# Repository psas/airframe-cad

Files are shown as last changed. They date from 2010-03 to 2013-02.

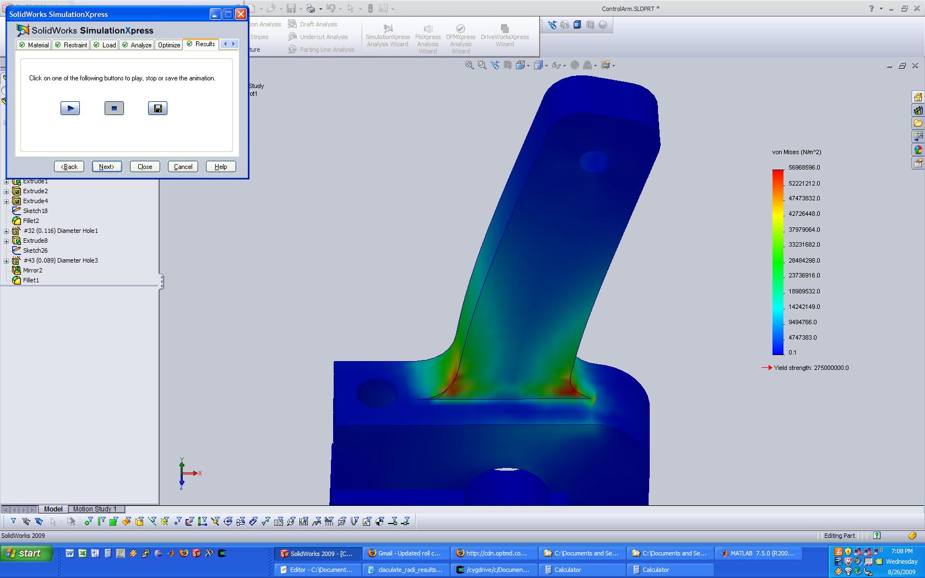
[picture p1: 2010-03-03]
sw_drawings/RollControl/FEA_Images/control_arm2.jpg

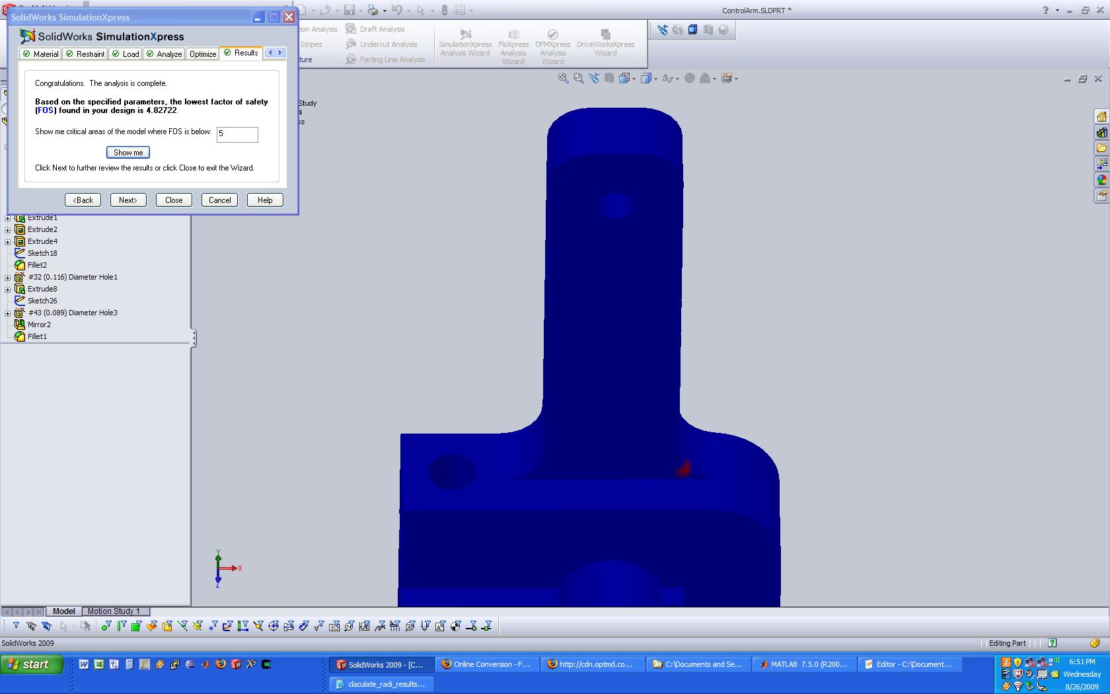
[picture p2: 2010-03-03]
sw_drawings/RollControl/FEA_Images/control_arm1.jpg

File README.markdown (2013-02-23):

# PSAS Airframe CAD files

Contains mostly solidworks files for the mechanical parts of our current rocket airframe.

 - [Airframe Team Home](http://psas.pdx.edu/airframe/)

You can download a free viewer from solidworks on their [downloads page](http://www.edrawingsviewer.com/ed/solidworks-viewer.htm).

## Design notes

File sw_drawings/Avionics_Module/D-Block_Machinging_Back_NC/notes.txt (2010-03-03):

1) uses 1/8 center drill
--X zero is the small flat side machined face of the endmost D-Block
--y-zero is the top face of the dblocks (back edge of vise) 
--z-zero is 1 inche above the machined faced side of the D-Block that were about to drill in

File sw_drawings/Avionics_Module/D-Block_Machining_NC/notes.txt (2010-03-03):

1) uses 1/2 roughing endmill
2-3) uses 1/2 finishing endmill
4) uses 1/8 center drill
5) uses 0.11dia drill

Zero is 1 inch above a piece of 0.5" x 5.0" x 2.0" flat bar, in the back-left corner of the stock

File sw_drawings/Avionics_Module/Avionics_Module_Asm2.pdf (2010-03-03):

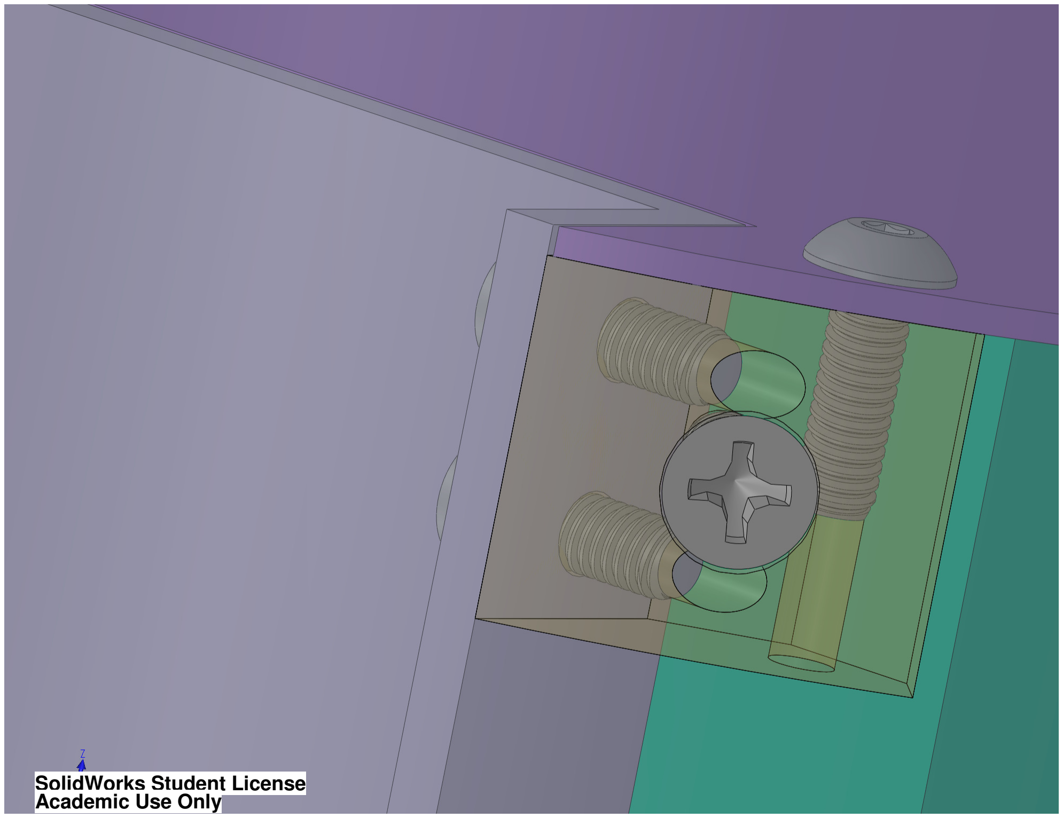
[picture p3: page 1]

SolidWorks Student License Academic Use Only

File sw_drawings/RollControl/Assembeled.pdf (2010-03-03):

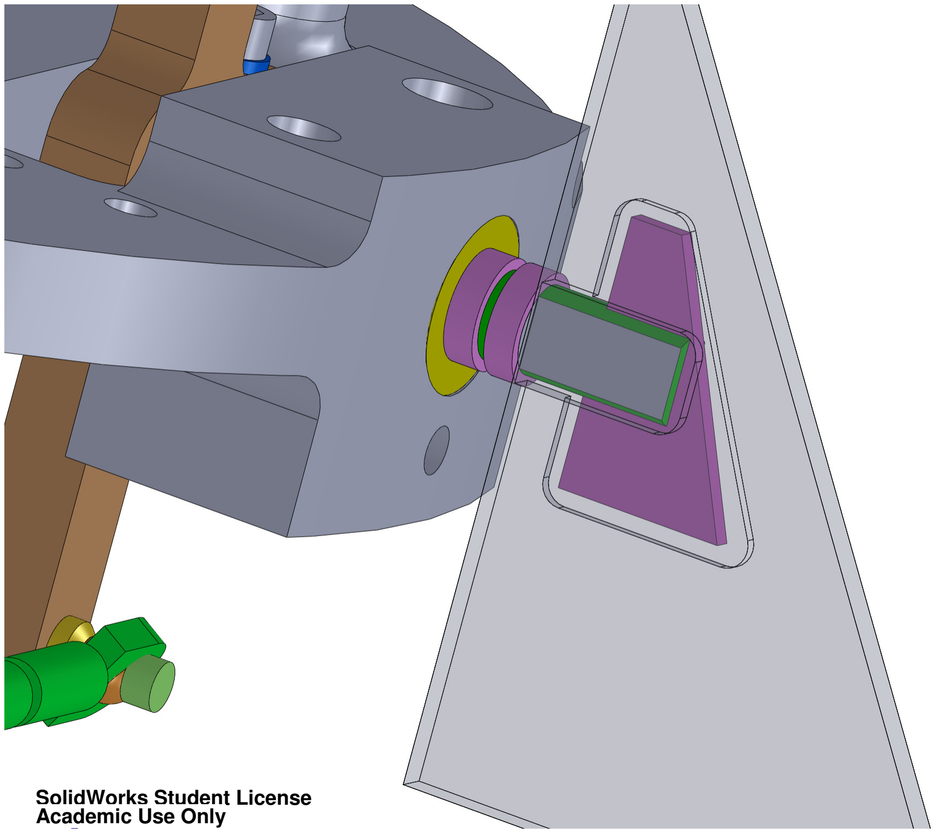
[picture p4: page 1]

SolidWorks Student License Academic Use Only

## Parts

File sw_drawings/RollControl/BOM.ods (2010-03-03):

Item | What for | Source | Source Part Number | Price | Qty | Ext Price
2-56 Dubro Swivel Ball Links | Linkage | Cyote Hobbies | LXAPC4 | $16.39 | 2 | $32.78
JR 8717 300hz Digital Servo | Linkage | Cyote Hobbies | JR 8717 | $109.00 | 1 | $109.00
1” by 0.375” 6061-T6 Flat bar, 3ft length | bell cranks | Master Carr | 8975K543 | $9.43 | 1 | $9.43
3mm screw, 18mm long, socket head cap screw | bell cranks | Master Carr | 91292A029 | $6.89 | 1 | $6.89
3mmID Tubing | bell cranks | Master Carr | 50415K158 | $11.65 | 1 | $11.65
3mmX6mmX2.5mm Ball Bearing | bell cranks | Master Carr | 7804K124 | $6.79 | 6 | $40.74
1/2” OD, 1/4” ID, 0.1875” thick ball bearings | Control Arm | Master Carr | 57155K376 | $5.10 | 8 | $40.80
1/4” ID Shaft Collar | Control Arm | Master Carr | 9414T6 | $0.58 | 4 | $2.32
1/4” OD Precision ground rod, hopefully machinable, 3ft section | Control Arm | Master Carr | 1144K16 |  | 1 | 0
4-40 Lock Nuts | Control Arm | Master Carr | 91831A005 | $3.95 | 1 | $3.95
4-40 socket head cap screw, 0.75” long | Control Arm | Master Carr | 92196A113 | $3.93 | 1 | $3.93
4-40 socket head cap screw, 1” long | Control Arm | Master Carr | 92196A115 | $4.00 | 1 | $4.00
4-40 Washers | Control Arm | Master Carr | 90945A711 | $13.05 | 1 | $13.05
Aluminum (Alloy 6061) Tube 1/2" OD, .402" ID, .049" Wall Thickness, 1' Length | Control Arm | Master Carr | 9056K653 | $5.96 | 1 | $5.96
Canard Spacer tubing | Control Arm | Master Carr | 8457K24 (http://www.mcmaster.com/itm/find.ASP?tab=find&context=psrchDtlLink&fasttrack=False&searchstring=8457K24) | $5.01 | 1 | $5.01
Woodruff Keys | Control Arm | Master Carr | 98525A050 | $6.01 | 1 | $6.01
2-56 Screws, 0.375” long, socket head cap | Linkage | Master Carr | 92196A079 | $3.72 | 1 | $3.72
2-56 Screws, 0.5” long, socket head cap | Linkage | Master Carr | 92196A081 | $3.97 | 1 | $3.97
2-56 Screws, 0.75” long, socket head cap | Linkage | Master Carr | 92196A084 | $4.64 | 1 | $4.64
2-56 Threaded rod, 1” sections | Linkage | Master Carr | 98804A003 | $1.72 | 1 | $1.72
2-56 Washers, a bag | Linkage | Master Carr | 98370A003 | $5.00 | 1 | $5.00
0.0625 thick, Silting saw that can do 0.671” deep, 3” or larger diameter | Tooling | Master Carr | 3061A35 | $23.60 | 1 | $23.60
C-2 Carbide Insert, 1/4" IC, 1/64" Radius | Tooling | Master Carr | 3240A132 | $5.13 | 2 | $10.26
Carbide-Insert Boring Tool 1/2" Shank Dia, 7/16" min Hole Dia, 2-1/8" D Max Bore | Tooling | Master Carr | 3249A202 | $25.59 | 1 | $25.59
Good 2-56 tap for aluminum | Tooling | Master Carr | 2636A116 | $12.40 | 1 | $12.40
Woodruff Cutter | Tooling | Master Carr | 3031A11 | $21.69 | 1 | $21.69
End mill, radius end mill, 0.125 radius, 0.5” dia, TiN | Tooling | MSC Direct | 8483075 | $69.03 | 1 | $69.03
End mill, TiN, 0.25” dia, standard end mill | Tooling | MSC Direct | 59517144 | $22.50 | 1 | $22.50
 |  |  |  |  |  |  |  | $499.64
6.0” OD, 1.75” thick, Aluminum 6061-T6 Round Bar | Base Plate | Metal Supermarkets |  | $18.17 | 1 | $18.17
3” x 0.25” x 36” 6061-T6 Flat Bar, if we need to machine control arms | Control Arm | Metal Supermarkets |  | $12.06 | 1 | $12.06
0.75” x 0.75” x 3ft 6061-T6 Square Bar | D-Blocks for mounting parts in modules | Metal Supermarkets |  | $8.89 | 1 | $8.89
18-8 Stainless Steel Nylon-Insert Hex Locknut 2-56 Thread Size, 1/4" Width, 9/64" Height | Linkage | Master Carr | 91831A002 | $13.62 | 1 | $13.62
E-Clips, Black-Phosphate Steel E-Style Retaining Ring for 1/4" Shaft Diameter | Control Arm | Master Carr | 97431A300 | $5.48 | 1 | $5.48
18-8 SS Precision Bearing Spacing Shim .020" Thick, .167" ID, .248" OD | Shims for aligning fins | Master Carr | 93574A213 | 7.81 | 1 | 7.81
8-8 SS Precision Bearing Spacing Shim .010" Thick, .167" ID, .248" OD | Shims for aligning fins | Master Carr | 93574A211 | 7.81 | 1 | 7.81
18-8 SS Precision Bearing Spacing Shim .005" Thick, .167" ID, .248" OD | Shims for aligning fins | Master Carr | 93574A207 | 7.81 | 1 | 7.81
 |  |  |  |  |  |  | $42.53
Plates for canards |  | Master Carr | 9517K112
Dubro Swivel Ball Links 2-56 (12) | Linkage | www.towerhobbies.com | LXAPC4 | $16.39 | 2 | $32.78

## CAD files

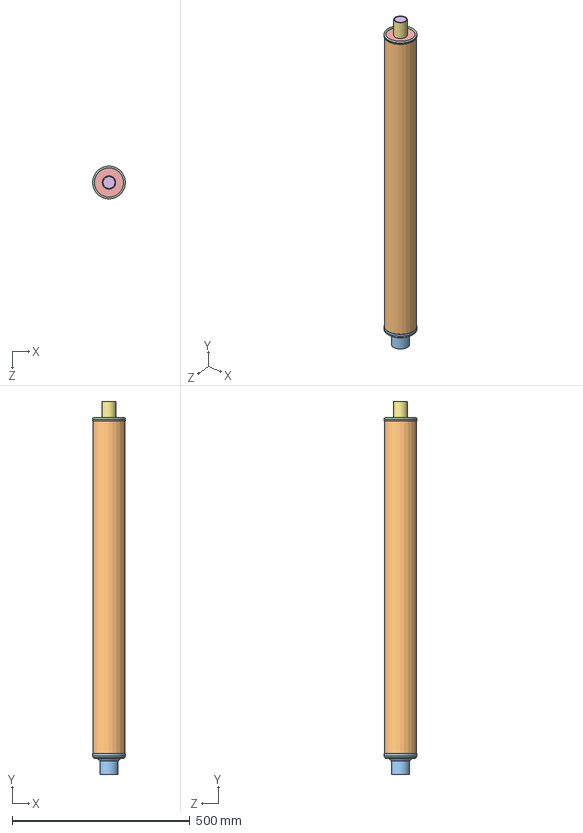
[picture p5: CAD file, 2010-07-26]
sw_drawings/Airframe_Drawings/N2000W_Motor_Reload/N2000W_Reload_Assembeled.SLDASM
92.2 x 1050.0 x 92.2 mm
N2000W_Grain x 6
N2000W_Reload_Liner
N2000W_Nozel
N2000W_O_Ring x 2
N2000W_Forward_Seal_Disc
N2000W_Smoke_Grain
N2000W_Smoke_Grain_Liner

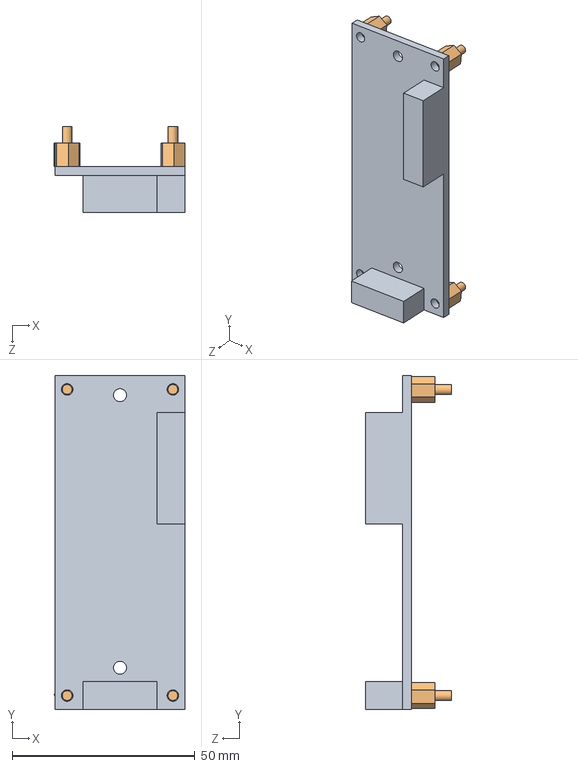
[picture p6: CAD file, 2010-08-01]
sw_drawings/Avionics/ARTS2_Flight_Computer_Asm.SLDASM
35.8 x 91.4 x 23.6 mm
ARTS2_Flight_Computer
0.25in_PCB_Standoff x 4

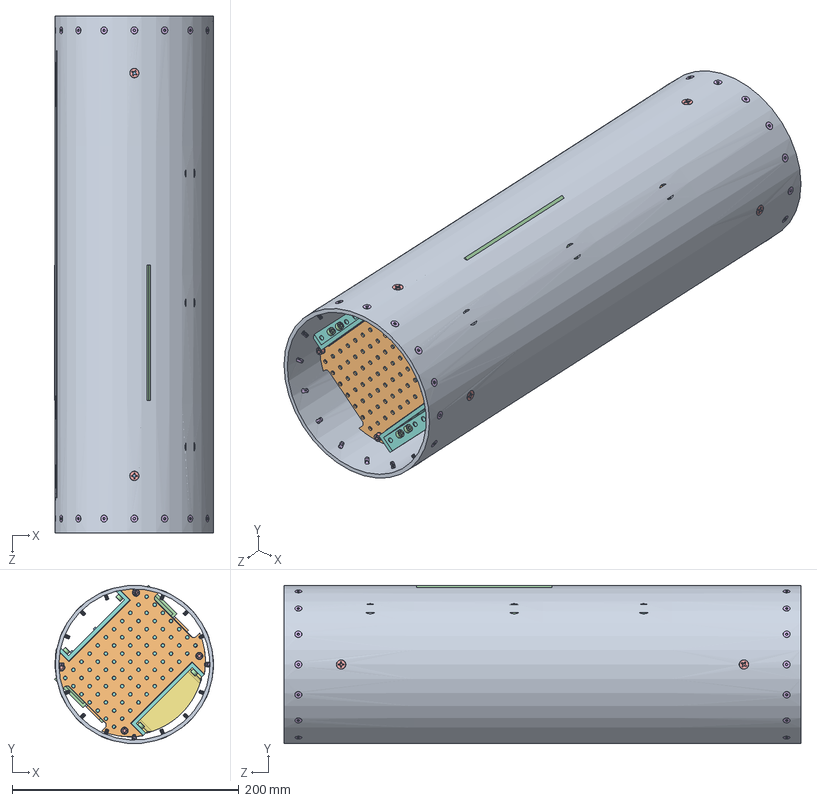
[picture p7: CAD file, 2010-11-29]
sw_drawings/Avionics_Module/Avionics_Module_Asm.SLDASM
140.5 x 139.9 x 456.4 mm
Avionics_Module_Plate2 x 3
D_Block_5 x 16
6-32_0.375in_Allen_Head_Cap_Screw_MC-91251A146 x 32
6-32_0.5in_Allen_Head_Cap_Screw_MC-91251A148 x 8
No_6_Steel_Wahser_MC-98032A436 x 8
RF_Sheild_Plate_SM
3in_x_0.6in_Channel_MC-9001K41 x 2
Mid_Plate
Mid_Plate_Angle x 2
4-40_Lock_Nut-MC-90631A005 x 8
Olimex_LPC2378
0.15in_Spacer x 4
4-40_0.3125in_Allen_Head_Cap_Screw_MC-91251A107 x 4
4-40_0.3125in_Pan_Head_Allen Cap_Screw_MC-91255A107 x 4
6-32_1.25in_Allen_Head_Cap_Screw_MC-91251A155 x 4
No_6_Steel_Wahser2_MC-94744A160 x 4
ARTS2_Flight_Computer
0.25in_PCB_Standoff x 4
Data_Logger
8-32_0.5in_Countersunk_Head_Allen_Screw-MC-91771A194_2 x 7
3.0mm_8mm_Counter_Sunk_Hex_Screw x 32
Battery_Box_Case
Battery_Box_Lid
Battery_Box_PCB_Board

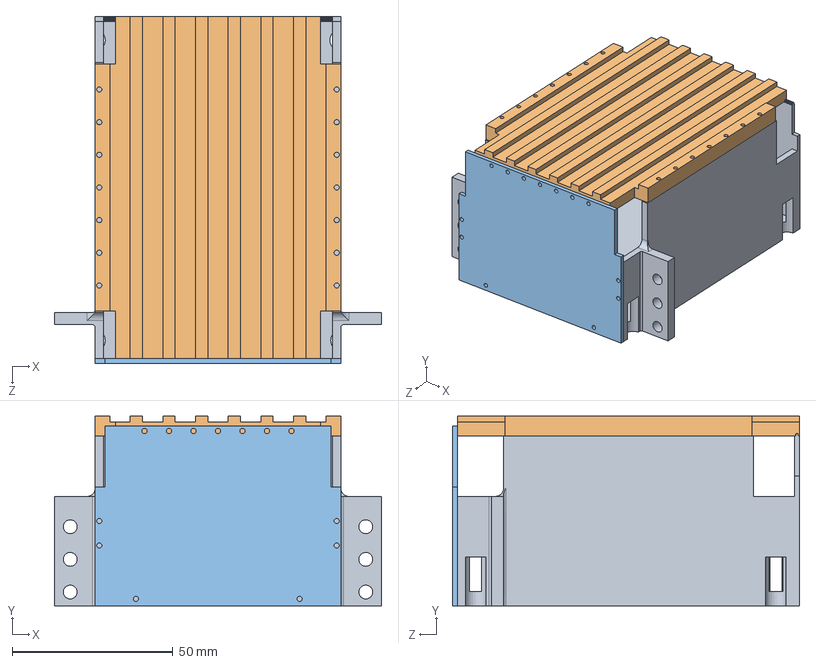
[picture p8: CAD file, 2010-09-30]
sw_drawings/Avionics_Module/Battery_Box/Battery_Box_Asm.SLDASM
101.9 x 59.1 x 108.0 mm
Battery_Box_Case
Battery_Box_Lid
Battery_Box_PCB_Board

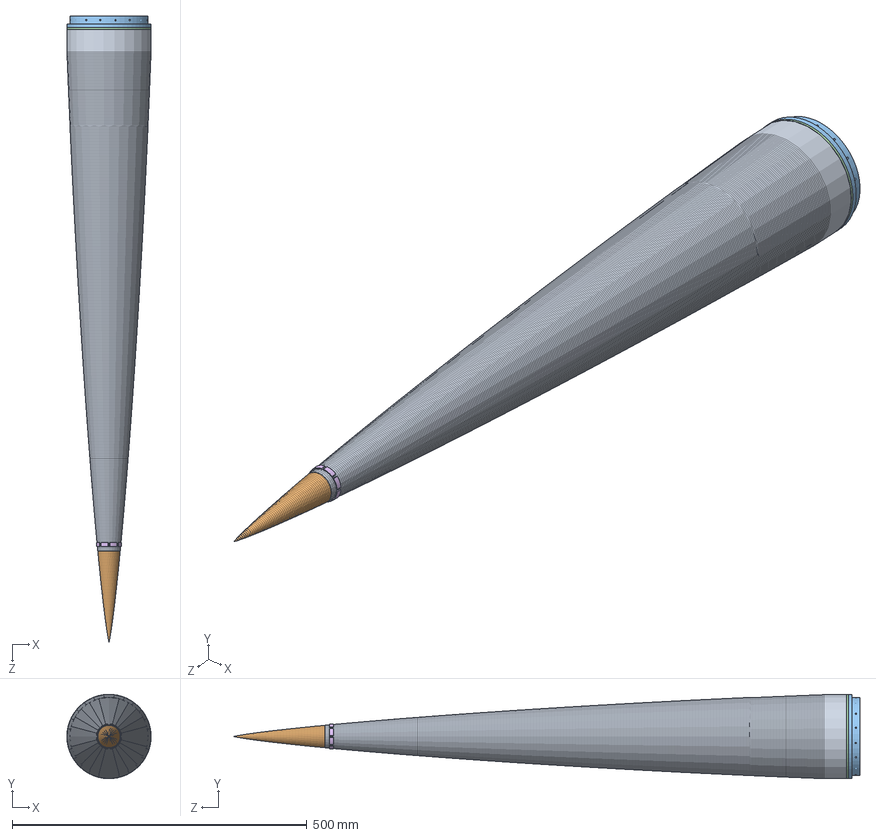
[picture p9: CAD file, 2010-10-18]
sw_drawings/Nosecone/Nosecone_Asm.SLDASM
143.1 x 143.1 x 1061.5 mm
Nosecone
Nosecone_Tip
NSR_Bottom
NSR_Top
Drogue_Parachute
Tip_Ring
Elastic_Outer_Ring
Pusher_Plate
Pusher_Tube
Upper_Elastic_Ring
Elastic x 23
8-32_Eyebolt

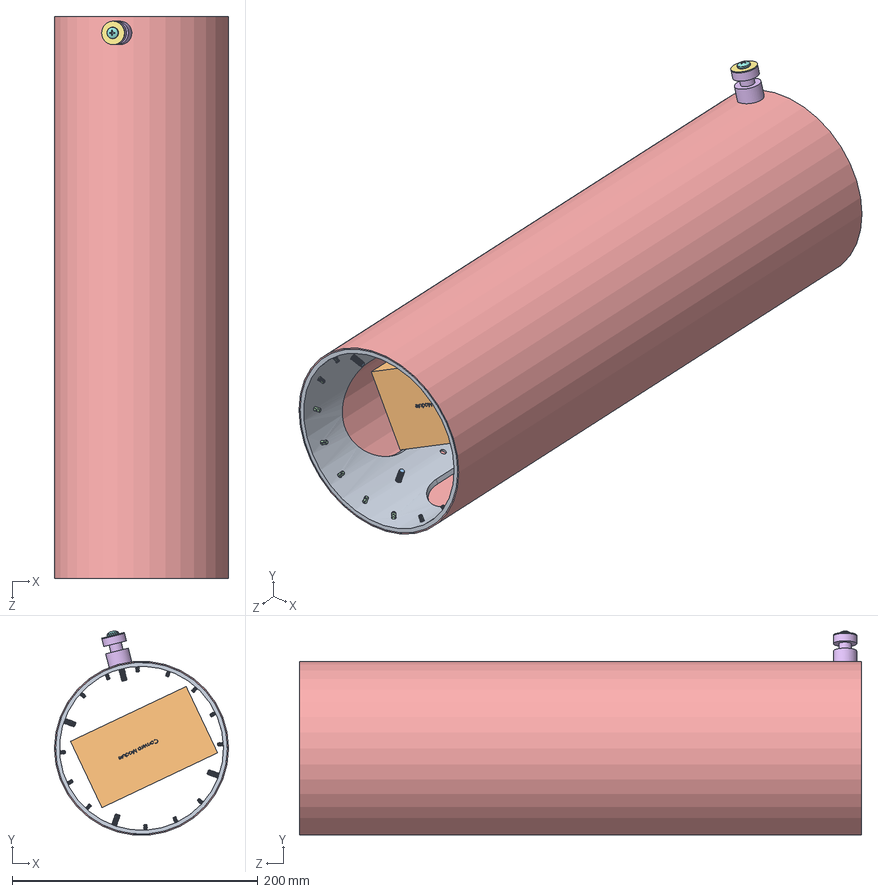
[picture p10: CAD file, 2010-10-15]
sw_drawings/Payload_Module/Payload_Module_Asm.SLDASM
141.6 x 165.9 x 457.2 mm
Module_Hollow
Camera_Module
8-32_0.5in_Countersunk_Head_Allen_Screw-MC-91771A194_2 x 6
3.0mm_8mm_Counter_Sunk_Hex_Screw x 32
Aeroshell_18
Launch_Lug
No_10_Steel_Fender_washer
10-32_1.5in_SS_Philips_Pan_Head_Screw

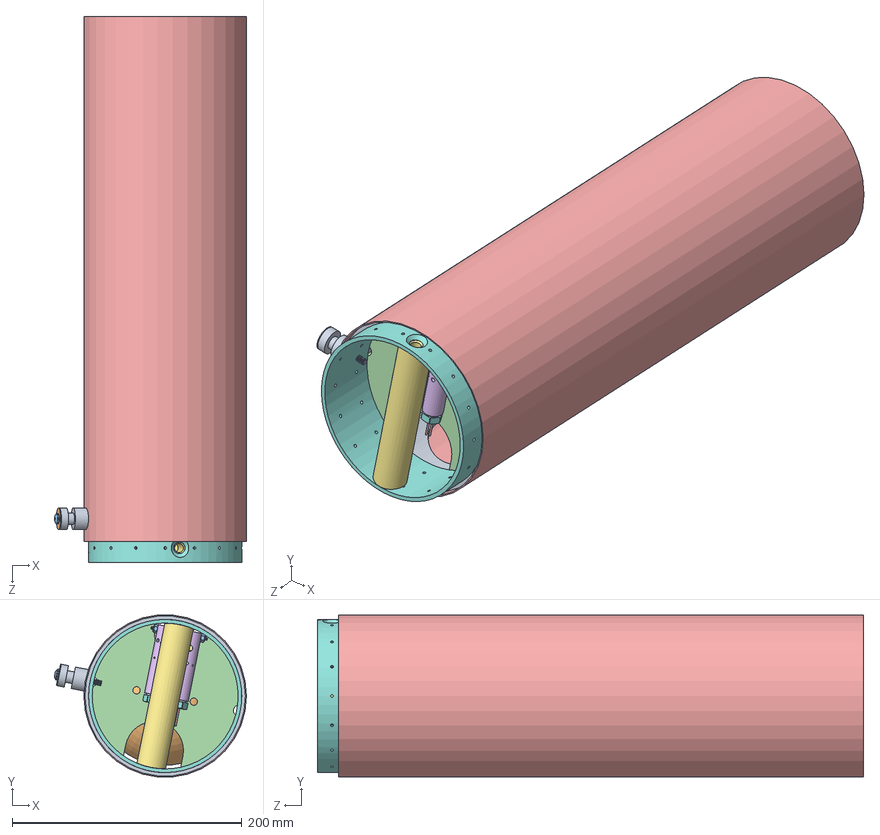
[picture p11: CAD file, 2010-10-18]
sw_drawings/Recovery_Module/Recovery_Module_Asm.SLDASM
167.2 x 141.0 x 475.5 mm
Module_Hollow_Short
Parachute
3.0mm_8mm_Counter_Sunk_Hex_Screw x 2
Shield_Plate
Line_Cutter_Body x 2
Cutter x 2
Modified_0.375in_x_0.5in_Hex_Head_Bolt x 2
Sealing_Washer x 2
Stop_Block x 2
4-40_Lock_Nut-MC-90631A005 x 2
4-40_0.875_Counter_Sunk_Cap_Screw x 2
Igniter_Lead_Wire x 4
Igniter x 2
Parachute_Cross_Bar
Module_Coupler_Recovery
Launch_Lug
No_10_Steel_Fender_washer
10-32_1.5in_SS_Philips_Pan_Head_Screw

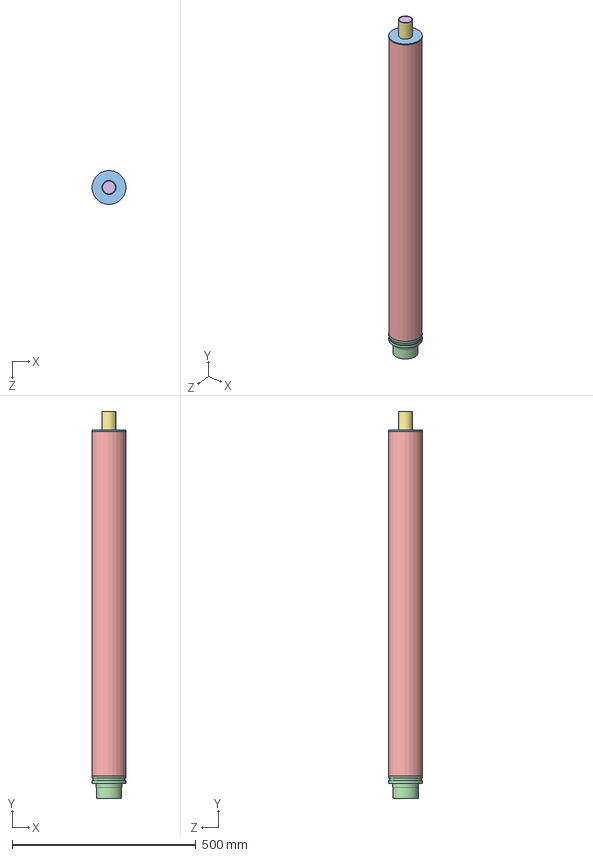
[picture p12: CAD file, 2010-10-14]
sw_drawings/Airframe_Drawings/N2850-P_Cesaroni_Reload/N2850_Reload_Asm.SLDASM
92.1 x 1052.3 x 92.1 mm
N2850P_Grain x 6
N2850P_Grain_O_Ring x 5
N2850P_Forward_Seal_Disc
N2850P_Nozel
N2850P_Reload_Liner
N2850P_Smoke_Grain
N2850P_Smoke_Grain_Liner

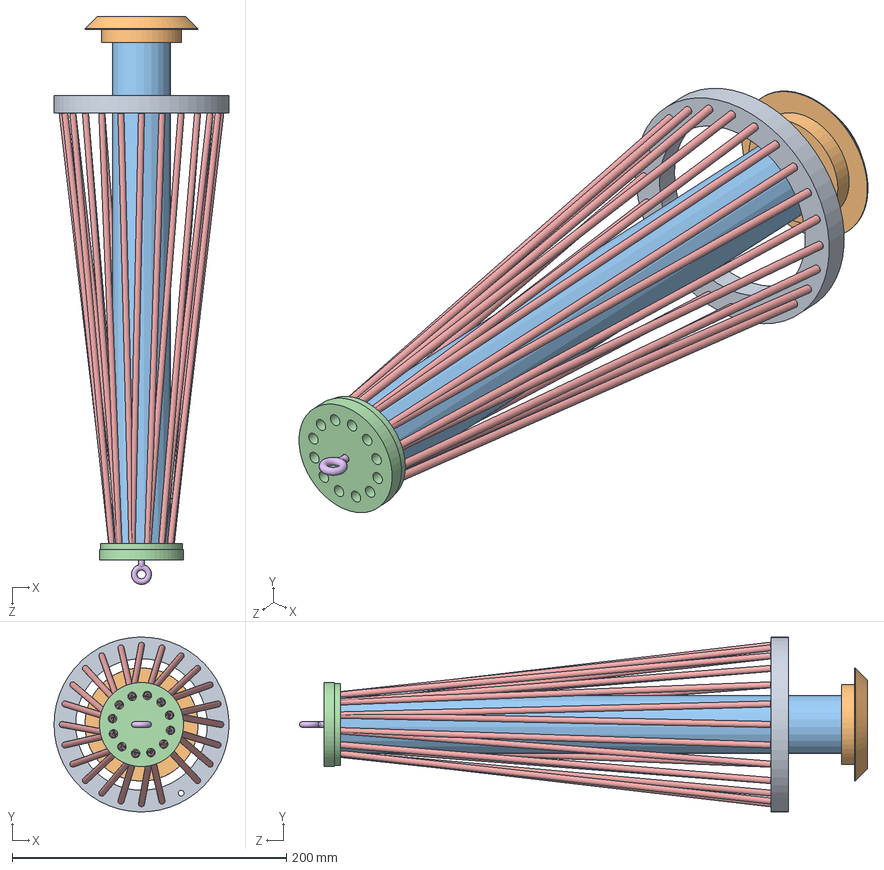
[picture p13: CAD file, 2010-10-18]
sw_drawings/Airframe_Drawings/Pusher_Rod/Pusher_Asm.SLDASM
127.7 x 127.6 x 414.5 mm
Elastic_Outer_Ring
Pusher_Plate
Pusher_Tube
Upper_Elastic_Ring
Elastic x 23
8-32_Eyebolt

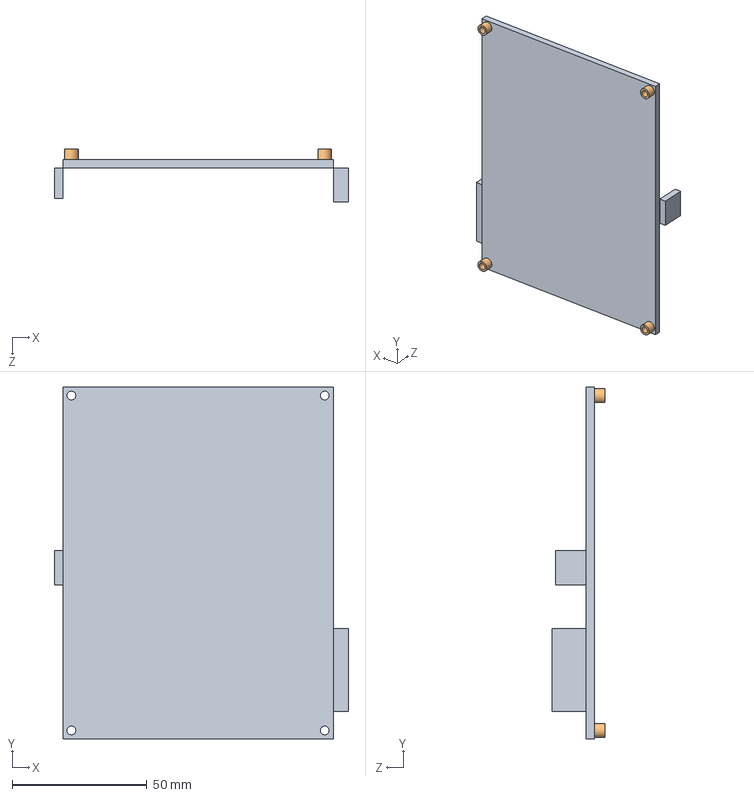
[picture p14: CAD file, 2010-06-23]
sw_drawings/Avionics/Olimex_2378_Asm.SLDASM
109.1 x 130.4 x 19.7 mm
Olimex_LPC2378
0.15in_Spacer x 4

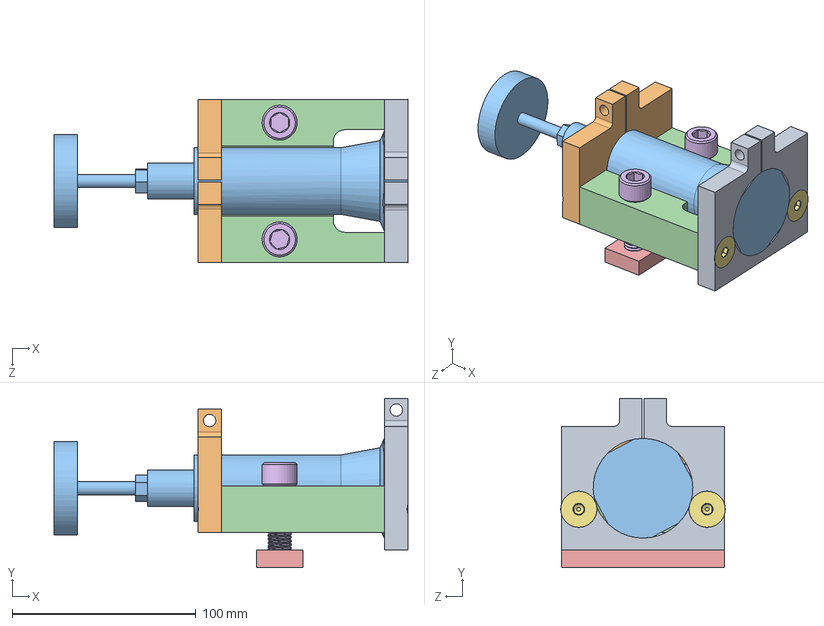
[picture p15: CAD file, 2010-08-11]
sw_drawings/Custom_Tools/Grinder_Mount/Toolpost_Grinder_Flat_Asm.SLDASM
192.7 x 92.1 x 89.6 mm
Large_Hole_Plate
Small_Hole_Plate
Grinder
Horozontal_Flat_Plate
Cross_Slide_Clamp
0.5in_1.5in_Long_Allen_Cap_Screw-91251A716 x 2
0.375in_1.0in_Countersunk_Allen_Screw x 2

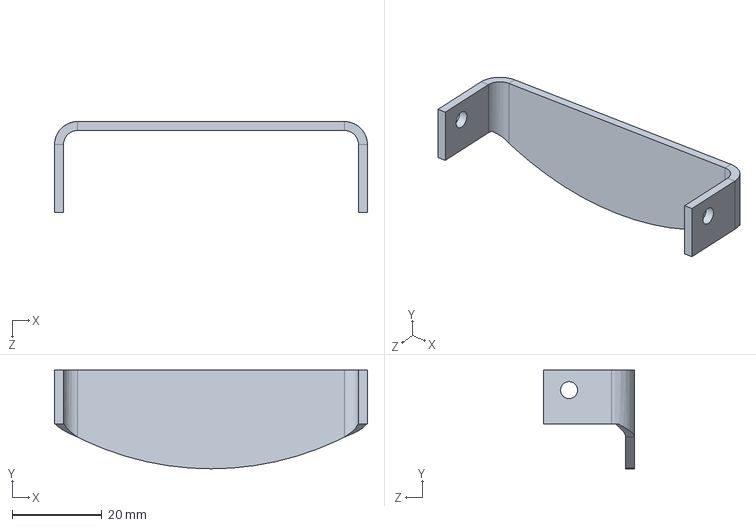
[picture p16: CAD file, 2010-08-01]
sw_drawings/Avionics_Module/RF_Plate_Asm.SLDASM
69.9 x 22.0 x 20.3 mm

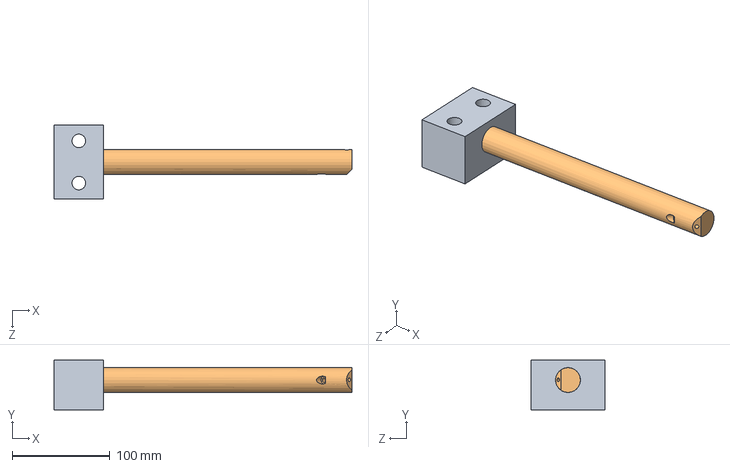
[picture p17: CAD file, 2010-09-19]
sw_drawings/Custom_Tools/Boring_Bar/Boring_Bar_Asm.SLDASM
304.8 x 50.8 x 76.2 mm
Bar_Cross_Slide_Mount
Bar

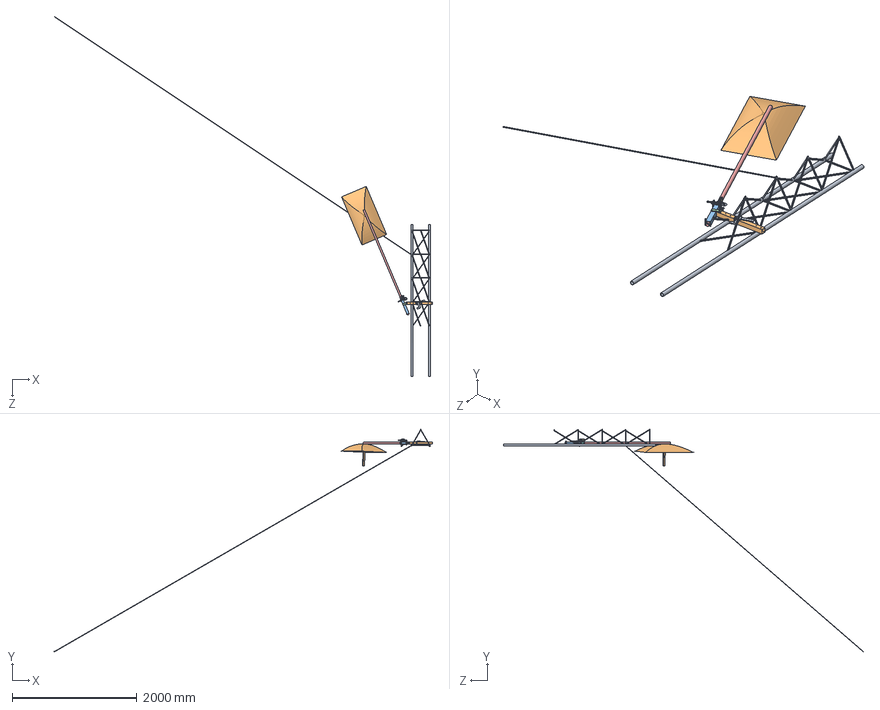
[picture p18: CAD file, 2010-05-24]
sw_drawings/Launch_Tower/Launch_Tower_Asm.SLDASM
6063.7 x 3569.1 x 5768.9 mm
Top_Tower
Lower_Tube
Outside_Tube
Pivit_Bar x 2
Antenna_Bar
Bar_Flat
Eye_Bolt_Holder
1.0in_U-Bolt x 2
0.375_Threaded_Eye_Bolt
0.375in-16_2.5in_Bolt
Stop_Spacer2
Top_Nut_Reference_Plate
Nut_Stop x 4
0.375_Hex_Nut x 2
Top_Bar_Latch_Lock
0.25-20_1.75in_Allen Head_Cap_Screw_MC-91251A548
Lock
Antenna
Guy_Wire

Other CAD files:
sw_drawings/Recovery_Module/Line_Cutters/Line_Cutter_Asm.SLDASM
sw_drawings/Payload_Module/Camera_System/Camear_Mount_Main_Base.SLDPRT
sw_drawings/Airframe_Drawings/Fin_and_Clamp_Asm.SLDASM
sw_drawings/Airframe_Drawings/Fin_Can_Rotation/Upper_Bearing_Asm.SLDASM
sw_drawings/Airframe_Drawings/0.25_Threaded_Rod_Hold_Plates.SLDPRT
sw_drawings/Airframe_Drawings/025in_Threaded_Rod.SLDPRT
sw_drawings/Airframe_Drawings/6-32_Barrel_Nut.SLDPRT
sw_drawings/Airframe_Drawings/Aerodynamics_Test_Bearing_Plate.SLDPRT
sw_drawings/Airframe_Drawings/Aeroshell_18.SLDPRT
sw_drawings/Airframe_Drawings/Aft_Motor_Centering_Ring.SLDPRT
sw_drawings/Airframe_Drawings/Aft_Motor_Centering_Ring_Thin.SLDDRW
sw_drawings/Airframe_Drawings/Aft_Motor_Centering_Ring_Thin.SLDPRT
sw_drawings/Airframe_Drawings/Copy of RouseTech_Motor_Retainmenta_Asm.SLDASM
sw_drawings/Airframe_Drawings/Fin.SLDDRW
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

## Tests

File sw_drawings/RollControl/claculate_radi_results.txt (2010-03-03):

.6331
.5819

                    bellCrankCenterRadi: 1.8500
                            servoRadius: 0.5750
             primaryBaseBellCrankRadius: 0.6331
                 primaryBellCrankRadius: 0.7331
               bellCrankAngularRotation: 67.3631
               secondaryBellCrankRadius: 0.5819
                       controlArmRadius: 1.5500
                controlArmAngleRotation: 24.0316
                       linkageRodLength: 1.3081
                    betaBellCrankRadius: 1.4168
                betaBellCrankBallRadius: 0.4732
                 betaBellCrankRodLength: 1.0018
               servoOunceInchesOfTorque: 128
                   servoBallForceOunces: 222.6087
    primaryBellCrankOunceInchesOfTorque: 140.9441
      secondaryBellCrankBallForceOunces: 242.2335
            controlArmTorqueOunceInches: 375.4619
                 controlArmForceNewtons: 104.3836

           bellCrankCenterRadi: 1.8500
                   servoRadius: 0.6750
    primaryBaseBellCrankRadius: 0.6331
        primaryBellCrankRadius: 0.6331
      bellCrankAngularRotation: 97.8496
      secondaryBellCrankRadius: 0.5819
              controlArmRadius: 1.2500
       controlArmAngleRotation: 41.0851
              linkageRodLength: 1.3081
           betaBellCrankRadius: 1.4168
       betaBellCrankBallRadius: 0.4732

ans = 

           bellCrankCenterRadi: 1.8500
                   servoRadius: 0.3750
    primaryBaseBellCrankRadius: 0.6331
        primaryBellCrankRadius: 0.9331
      bellCrankAngularRotation: 33.0175
      secondaryBellCrankRadius: 0.5819
              controlArmRadius: 0.6500
       controlArmAngleRotation: 29.4725
              linkageRodLength: 1.3081

CHOOSEN
ans = 

           bellCrankCenterRadi: 1.8500
                   servoRadius: 0.3750
    primaryBaseBellCrankRadius: 0.6331
        primaryBellCrankRadius: 0.9331
      bellCrankAngularRotation: 33.0175
      secondaryBellCrankRadius: 0.5819
              controlArmRadius: 0.7500
       controlArmAngleRotation: 25.4714
              linkageRodLength: 1.3081

ans = 

           bellCrankCenterRadi: 1.8500
                   servoRadius: 0.3750
    primaryBaseBellCrankRadius: 0.6331
        primaryBellCrankRadius: 0.9331
      bellCrankAngularRotation: 33.0175
      secondaryBellCrankRadius: 0.5819
              controlArmRadius: 0.8500
       controlArmAngleRotation: 22.4331
              linkageRodLength: 1.3081

ans = 

           bellCrankCenterRadi: 1.8500
                   servoRadius: 0.4750
    primaryBaseBellCrankRadius: 0.6331
        primaryBellCrankRadius: 0.8331
      bellCrankAngularRotation: 47.5493
      secondaryBellCrankRadius: 0.5819
              controlArmRadius: 0.6500
       controlArmAngleRotation: 42.3078
              linkageRodLength: 1.3081

ans = 

           bellCrankCenterRadi: 1.8500
                   servoRadius: 0.4750
    primaryBaseBellCrankRadius: 0.6331
        primaryBellCrankRadius: 0.8331
      bellCrankAngularRotation: 47.5493
      secondaryBellCrankRadius: 0.5819
              controlArmRadius: 0.7500
       controlArmAngleRotation: 36.4510
              linkageRodLength: 1.3081

ans = 

           bellCrankCenterRadi: 1.8500
                   servoRadius: 0.4750
    primaryBaseBellCrankRadius: 0.6331
        primaryBellCrankRadius: 0.8331
      bellCrankAngularRotation: 47.5493
      secondaryBellCrankRadius: 0.5819
              controlArmRadius: 0.8500
       controlArmAngleRotation: 32.0388
              linkageRodLength: 1.3081

ans = 

           bellCrankCenterRadi: 1.8500
                   servoRadius: 0.5750
    primaryBaseBellCrankRadius: 0.6331
        primaryBellCrankRadius: 0.7331
      bellCrankAngularRotation: 67.3631
      secondaryBellCrankRadius: 0.5819
              controlArmRadius: 0.8500
       controlArmAngleRotation: 44.6210
              linkageRodLength: 1.3081

ans = 

           bellCrankCenterRadi: 1.9000
                   servoRadius: 0.3750
    primaryBaseBellCrankRadius: 0.6685
        primaryBellCrankRadius: 0.9685
      bellCrankAngularRotation: 31.7797
      secondaryBellCrankRadius: 0.5465
              controlArmRadius: 0.6500
       controlArmAngleRotation: 26.6167
              linkageRodLength: 1.3435

ans = 

           bellCrankCenterRadi: 1.9000
                   servoRadius: 0.3750
    primaryBaseBellCrankRadius: 0.6685
        primaryBellCrankRadius: 0.9685
      bellCrankAngularRotation: 31.7797
      secondaryBellCrankRadius: 0.5465
              controlArmRadius: 0.7500
       controlArmAngleRotation: 23.0154
              linkageRodLength: 1.3435

ans = 

           bellCrankCenterRadi: 1.9000
                   servoRadius: 0.3750
    primaryBaseBellCrankRadius: 0.6685
        primaryBellCrankRadius: 0.9685
      bellCrankAngularRotation: 31.7797
      secondaryBellCrankRadius: 0.5465
              controlArmRadius: 0.8500
       controlArmAngleRotation: 20.2771
              linkageRodLength: 1.3435

ans = 

           bellCrankCenterRadi: 1.9000
                   servoRadius: 0.4750
    primaryBaseBellCrankRadius: 0.6685
        primaryBellCrankRadius: 0.8685
      bellCrankAngularRotation: 45.5023
      secondaryBellCrankRadius: 0.5465
              controlArmRadius: 0.6500
       controlArmAngleRotation: 37.9492
              linkageRodLength: 1.3435

ans = 

           bellCrankCenterRadi: 1.9000
                   servoRadius: 0.4750
    primaryBaseBellCrankRadius: 0.6685
        primaryBellCrankRadius: 0.8685
      bellCrankAngularRotation: 45.5023
      secondaryBellCrankRadius: 0.5465
              controlArmRadius: 0.7500
       controlArmAngleRotation: 32.7348
              linkageRodLength: 1.3435

ans = 

           bellCrankCenterRadi: 1.9000
                   servoRadius: 0.4750
    primaryBaseBellCrankRadius: 0.6685
        primaryBellCrankRadius: 0.8685
      bellCrankAngularRotation: 45.5023
      secondaryBellCrankRadius: 0.5465
              controlArmRadius: 0.8500
       controlArmAngleRotation: 28.7945
              linkageRodLength: 1.3435

ans = 

           bellCrankCenterRadi: 1.9000
                   servoRadius: 0.5750
    primaryBaseBellCrankRadius: 0.6685
        primaryBellCrankRadius: 0.7685
      bellCrankAngularRotation: 63.8843
      secondaryBellCrankRadius: 0.5465
              controlArmRadius: 0.8500
       controlArmAngleRotation: 39.7726
              linkageRodLength: 1.3435

ans = 

           bellCrankCenterRadi: 1.9500
                   servoRadius: 0.3750
    primaryBaseBellCrankRadius: 0.7039
        primaryBellCrankRadius: 1.0039
      bellCrankAngularRotation: 30.6324
      secondaryBellCrankRadius: 0.5111
              controlArmRadius: 0.6500
       controlArmAngleRotation: 23.9772
              linkageRodLength: 1.3789

ans = 

           bellCrankCenterRadi: 1.9500
                   servoRadius: 0.3750
    primaryBaseBellCrankRadius: 0.7039
        primaryBellCrankRadius: 1.0039
      bellCrankAngularRotation: 30.6324
      secondaryBellCrankRadius: 0.5111
              controlArmRadius: 0.7500
       controlArmAngleRotation: 20.7420
              linkageRodLength: 1.3789

ans = 

           bellCrankCenterRadi: 1.9500
                   servoRadius: 0.4750
    primaryBaseBellCrankRadius: 0.7039
        primaryBellCrankRadius: 0.9039
      bellCrankAngularRotation: 43.6289
      secondaryBellCrankRadius: 0.5111
              controlArmRadius: 0.6500
       controlArmAngleRotation: 33.9815
              linkageRodLength: 1.3789

ans = 

           bellCrankCenterRadi: 1.9500
                   servoRadius: 0.4750
    primaryBaseBellCrankRadius: 0.7039
        primaryBellCrankRadius: 0.9039
      bellCrankAngularRotation: 43.6289
      secondaryBellCrankRadius: 0.5111
              controlArmRadius: 0.7500
       controlArmAngleRotation: 29.3404
              linkageRodLength: 1.3789

ans = 

           bellCrankCenterRadi: 1.9500
                   servoRadius: 0.4750
    primaryBaseBellCrankRadius: 0.7039
        primaryBellCrankRadius: 0.9039
      bellCrankAngularRotation: 43.6289
      secondaryBellCrankRadius: 0.5111
              controlArmRadius: 0.8500
       controlArmAngleRotation: 25.8247
              linkageRodLength: 1.3789

ans = 

           bellCrankCenterRadi: 1.9500
                   servoRadius: 0.5750
    primaryBaseBellCrankRadius: 0.7039
        primaryBellCrankRadius: 0.8039
      bellCrankAngularRotation: 60.7681
      secondaryBellCrankRadius: 0.5111
              controlArmRadius: 0.7500
       controlArmAngleRotation: 40.3282
              linkageRodLength: 1.3789

ans = 

           bellCrankCenterRadi: 1.9500
                   servoRadius: 0.5750
    primaryBaseBellCrankRadius: 0.7039
        primaryBellCrankRadius: 0.8039
      bellCrankAngularRotation: 60.7681
      secondaryBellCrankRadius: 0.5111
              controlArmRadius: 0.8500
       controlArmAngleRotation: 35.4147
              linkageRodLength: 1.3789

ans = 

           bellCrankCenterRadi: 2
                   servoRadius: 0.3750
    primaryBaseBellCrankRadius: 0.7392
        primaryBellCrankRadius: 1.0392
      bellCrankAngularRotation: 29.5661
      secondaryBellCrankRadius: 0.4758
              controlArmRadius: 0.6500
       controlArmAngleRotation: 21.5288
              linkageRodLength: 1.4142

ans = 

           bellCrankCenterRadi: 2
                   servoRadius: 0.4750
    primaryBaseBellCrankRadius: 0.7392
        primaryBellCrankRadius: 0.9392
      bellCrankAngularRotation: 41.9074
      secondaryBellCrankRadius: 0.4758
              controlArmRadius: 0.6500
       controlArmAngleRotation: 30.3497
              linkageRodLength: 1.4142

ans = 

           bellCrankCenterRadi: 2
                   servoRadius: 0.4750
    primaryBaseBellCrankRadius: 0.7392
        primaryBellCrankRadius: 0.9392
      bellCrankAngularRotation: 41.9074
      secondaryBellCrankRadius: 0.4758
              controlArmRadius: 0.7500
       controlArmAngleRotation: 26.2250
              linkageRodLength: 1.4142

ans = 

           bellCrankCenterRadi: 2
                   servoRadius: 0.4750
    primaryBaseBellCrankRadius: 0.7392
        primaryBellCrankRadius: 0.9392
      bellCrankAngularRotation: 41.9074
      secondaryBellCrankRadius: 0.4758
              controlArmRadius: 0.8500
       controlArmAngleRotation: 23.0943
              linkageRodLength: 1.4142

ans = 

           bellCrankCenterRadi: 2
                   servoRadius: 0.5750
    primaryBaseBellCrankRadius: 0.7392
        primaryBellCrankRadius: 0.8392
      bellCrankAngularRotation: 57.9575
      secondaryBellCrankRadius: 0.4758
              controlArmRadius: 0.6500
       controlArmAngleRotation: 41.5419
              linkageRodLength: 1.4142

ans = 

           bellCrankCenterRadi: 2
                   servoRadius: 0.5750
    primaryBaseBellCrankRadius: 0.7392
        primaryBellCrankRadius: 0.8392
      bellCrankAngularRotation: 57.9575
      secondaryBellCrankRadius: 0.4758
              controlArmRadius: 0.7500
       controlArmAngleRotation: 35.7990
              linkageRodLength: 1.4142

ans = 

           bellCrankCenterRadi: 2
                   servoRadius: 0.5750
    primaryBaseBellCrankRadius: 0.7392
        primaryBellCrankRadius: 0.8392
      bellCrankAngularRotation: 57.9575
      secondaryBellCrankRadius: 0.4758
              controlArmRadius: 0.8500
       controlArmAngleRotation: 31.4702
              linkageRodLength: 1.4142

ans = 

           bellCrankCenterRadi: 2
                   servoRadius: 0.6750
    primaryBaseBellCrankRadius: 0.7392
        primaryBellCrankRadius: 0.7392
      bellCrankAngularRotation: 80.4337
      secondaryBellCrankRadius: 0.4758
              controlArmRadius: 0.8500
       controlArmAngleRotation: 42.3748
              linkageRodLength: 1.4142

ans = 

           bellCrankCenterRadi: 2.0500
                   servoRadius: 0.4750
    primaryBaseBellCrankRadius: 0.7746
        primaryBellCrankRadius: 0.9746
      bellCrankAngularRotation: 40.3197
      secondaryBellCrankRadius: 0.4404
              controlArmRadius: 0.6500
       controlArmAngleRotation: 27.0092
              linkageRodLength: 1.4496

ans = 

           bellCrankCenterRadi: 2.0500
                   servoRadius: 0.4750
    primaryBaseBellCrankRadius: 0.7746
        primaryBellCrankRadius: 0.9746
      bellCrankAngularRotation: 40.3197
      secondaryBellCrankRadius: 0.4404
              controlArmRadius: 0.7500
       controlArmAngleRotation: 23.3532
              linkageRodLength: 1.4496

ans = 

           bellCrankCenterRadi: 2.0500
                   servoRadius: 0.4750
    primaryBaseBellCrankRadius: 0.7746
        primaryBellCrankRadius: 0.9746
      bellCrankAngularRotation: 40.3197
      secondaryBellCrankRadius: 0.4404
              controlArmRadius: 0.8500
       controlArmAngleRotation: 20.5738
              linkageRodLength: 1.4496

ans = 

           bellCrankCenterRadi: 2.0500
                   servoRadius: 0.5750
    primaryBaseBellCrankRadius: 0.7746
        primaryBellCrankRadius: 0.8746
      bellCrankAngularRotation: 55.4074
      secondaryBellCrankRadius: 0.4404
              controlArmRadius: 0.6500
       controlArmAngleRotation: 36.7228
              linkageRodLength: 1.4496

ans = 

           bellCrankCenterRadi: 2.0500
                   servoRadius: 0.5750
    primaryBaseBellCrankRadius: 0.7746
        primaryBellCrankRadius: 0.8746
      bellCrankAngularRotation: 55.4074
      secondaryBellCrankRadius: 0.4404
              controlArmRadius: 0.7500
       controlArmAngleRotation: 31.6867
              linkageRodLength: 1.4496

ans = 

           bellCrankCenterRadi: 2.0500
                   servoRadius: 0.5750
    primaryBaseBellCrankRadius: 0.7746
        primaryBellCrankRadius: 0.8746
      bellCrankAngularRotation: 55.4074
      secondaryBellCrankRadius: 0.4404
              controlArmRadius: 0.8500
       controlArmAngleRotation: 27.8781
              linkageRodLength: 1.4496

ans = 

           bellCrankCenterRadi: 2.0500
                   servoRadius: 0.6750
    primaryBaseBellCrankRadius: 0.7746
        primaryBellCrankRadius: 0.7746
      bellCrankAngularRotation: 76.0798
      secondaryBellCrankRadius: 0.4404
              controlArmRadius: 0.7500
       controlArmAngleRotation: 42.4294
              linkageRodLength: 1.4496

ans = 

           bellCrankCenterRadi: 2.0500
                   servoRadius: 0.6750
    primaryBaseBellCrankRadius: 0.7746
        primaryBellCrankRadius: 0.7746
      bellCrankAngularRotation: 76.0798
      secondaryBellCrankRadius: 0.4404
              controlArmRadius: 0.8500
       controlArmAngleRotation: 37.2402
              linkageRodLength: 1.4496

ans = 

           bellCrankCenterRadi: 2.1000
                   servoRadius: 0.4750
    primaryBaseBellCrankRadius: 0.8099
        primaryBellCrankRadius: 1.0099
      bellCrankAngularRotation: 38.8503
      secondaryBellCrankRadius: 0.4051
              controlArmRadius: 0.6500
       controlArmAngleRotation: 23.9235
              linkageRodLength: 1.4849

ans = 

           bellCrankCenterRadi: 2.1000
                   servoRadius: 0.4750
    primaryBaseBellCrankRadius: 0.8099
        primaryBellCrankRadius: 1.0099
      bellCrankAngularRotation: 38.8503
      secondaryBellCrankRadius: 0.4051
              controlArmRadius: 0.7500
       controlArmAngleRotation: 20.6957
              linkageRodLength: 1.4849

ans = 

           bellCrankCenterRadi: 2.1000
                   servoRadius: 0.5750
    primaryBaseBellCrankRadius: 0.8099
        primaryBellCrankRadius: 0.9099
      bellCrankAngularRotation: 53.0817
      secondaryBellCrankRadius: 0.4051
              controlArmRadius: 0.6500
       controlArmAngleRotation: 32.3372
              linkageRodLength: 1.4849

ans = 

           bellCrankCenterRadi: 2.1000
                   servoRadius: 0.5750
    primaryBaseBellCrankRadius: 0.8099
        primaryBellCrankRadius: 0.9099
      bellCrankAngularRotation: 53.0817
      secondaryBellCrankRadius: 0.4051
              controlArmRadius: 0.7500
       controlArmAngleRotation: 27.9308
              linkageRodLength: 1.4849

ans = 

           bellCrankCenterRadi: 2.1000
                   servoRadius: 0.5750
    primaryBaseBellCrankRadius: 0.8099
        primaryBellCrankRadius: 0.9099
      bellCrankAngularRotation: 53.0817
      secondaryBellCrankRadius: 0.4051
              controlArmRadius: 0.8500
       controlArmAngleRotation: 24.5898
              linkageRodLength: 1.4849

ans = 

           bellCrankCenterRadi: 2.1000
                   servoRadius: 0.6750
    primaryBaseBellCrankRadius: 0.8099
        primaryBellCrankRadius: 0.8099
      bellCrankAngularRotation: 72.2162
      secondaryBellCrankRadius: 0.4051
              controlArmRadius: 0.6500
       controlArmAngleRotation: 43.0928
              linkageRodLength: 1.4849

ans = 

           bellCrankCenterRadi: 2.1000
                   servoRadius: 0.6750
    primaryBaseBellCrankRadius: 0.8099
        primaryBellCrankRadius: 0.8099
      bellCrankAngularRotation: 72.2162
      secondaryBellCrankRadius: 0.4051
              controlArmRadius: 0.7500
       controlArmAngleRotation: 37.1188
              linkageRodLength: 1.4849

ans = 

           bellCrankCenterRadi: 2.1000
                   servoRadius: 0.6750
    primaryBaseBellCrankRadius: 0.8099
        primaryBellCrankRadius: 0.8099
      bellCrankAngularRotation: 72.2162
      secondaryBellCrankRadius: 0.4051
              controlArmRadius: 0.8500
       controlArmAngleRotation: 32.6209
              linkageRodLength: 1.4849

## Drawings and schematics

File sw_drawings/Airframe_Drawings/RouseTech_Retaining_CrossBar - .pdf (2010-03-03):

1.000

.375

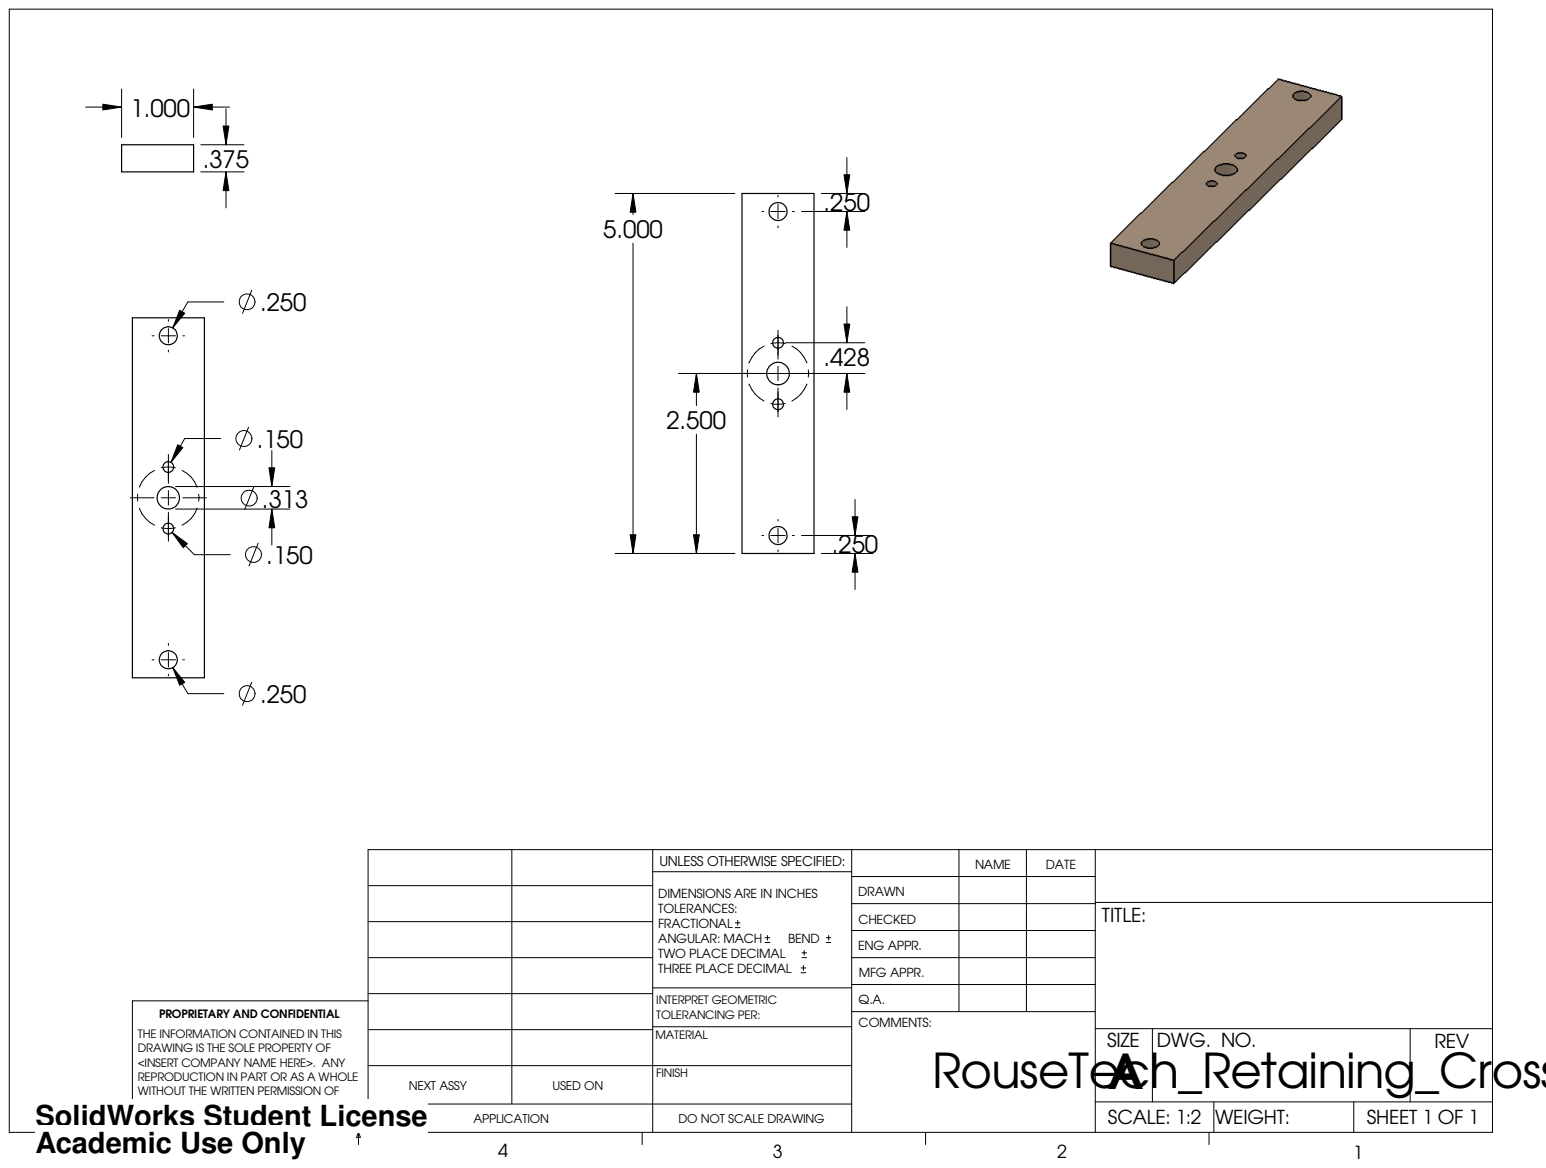
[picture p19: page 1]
RouseTech_Retaining_Cross; COMMENTS:; BEND

UNLESS OTHERWISE SPECIFIED: | | NAME | DATE

DIMENSIONS ARE IN INCHES
TOLERANCES:
FRACTIONAL
ANGULAR: MACH
TWO PLACE DECIMAL
THREE PLACE DECIMAL

DRAWN
CHECKED | | | TITLE:

ENG APPR.

MFG APPR.

INTERPRET GEOMETRIC TOLERANCING PER: | Q.A.
MATERIAL | | SIZE A | DWG. NO. | REV

PROPRIETARY AND CONFIDENTIAL
THE INFORMATION CONTAINED IN THIS
DRAWING IS THE SOLE PROPERTY OF
<INSERT COMPANY NAME HERE>. ANY
REPRODUCTION IN PART OR AS A WHOLE
WITHOUT THE WRITTEN PERMISSION OF
<INSERT COMPANY NAME HERE> IS
PROHIBITED.

NEXT ASSY | USED ON | FINISH

SolidWorks Student License
Academic Use Only

APPLICATION | DO NOT SCALE DRAWING | | SCALE: 1:2 | WEIGHT: | SHEET 1 OF 1

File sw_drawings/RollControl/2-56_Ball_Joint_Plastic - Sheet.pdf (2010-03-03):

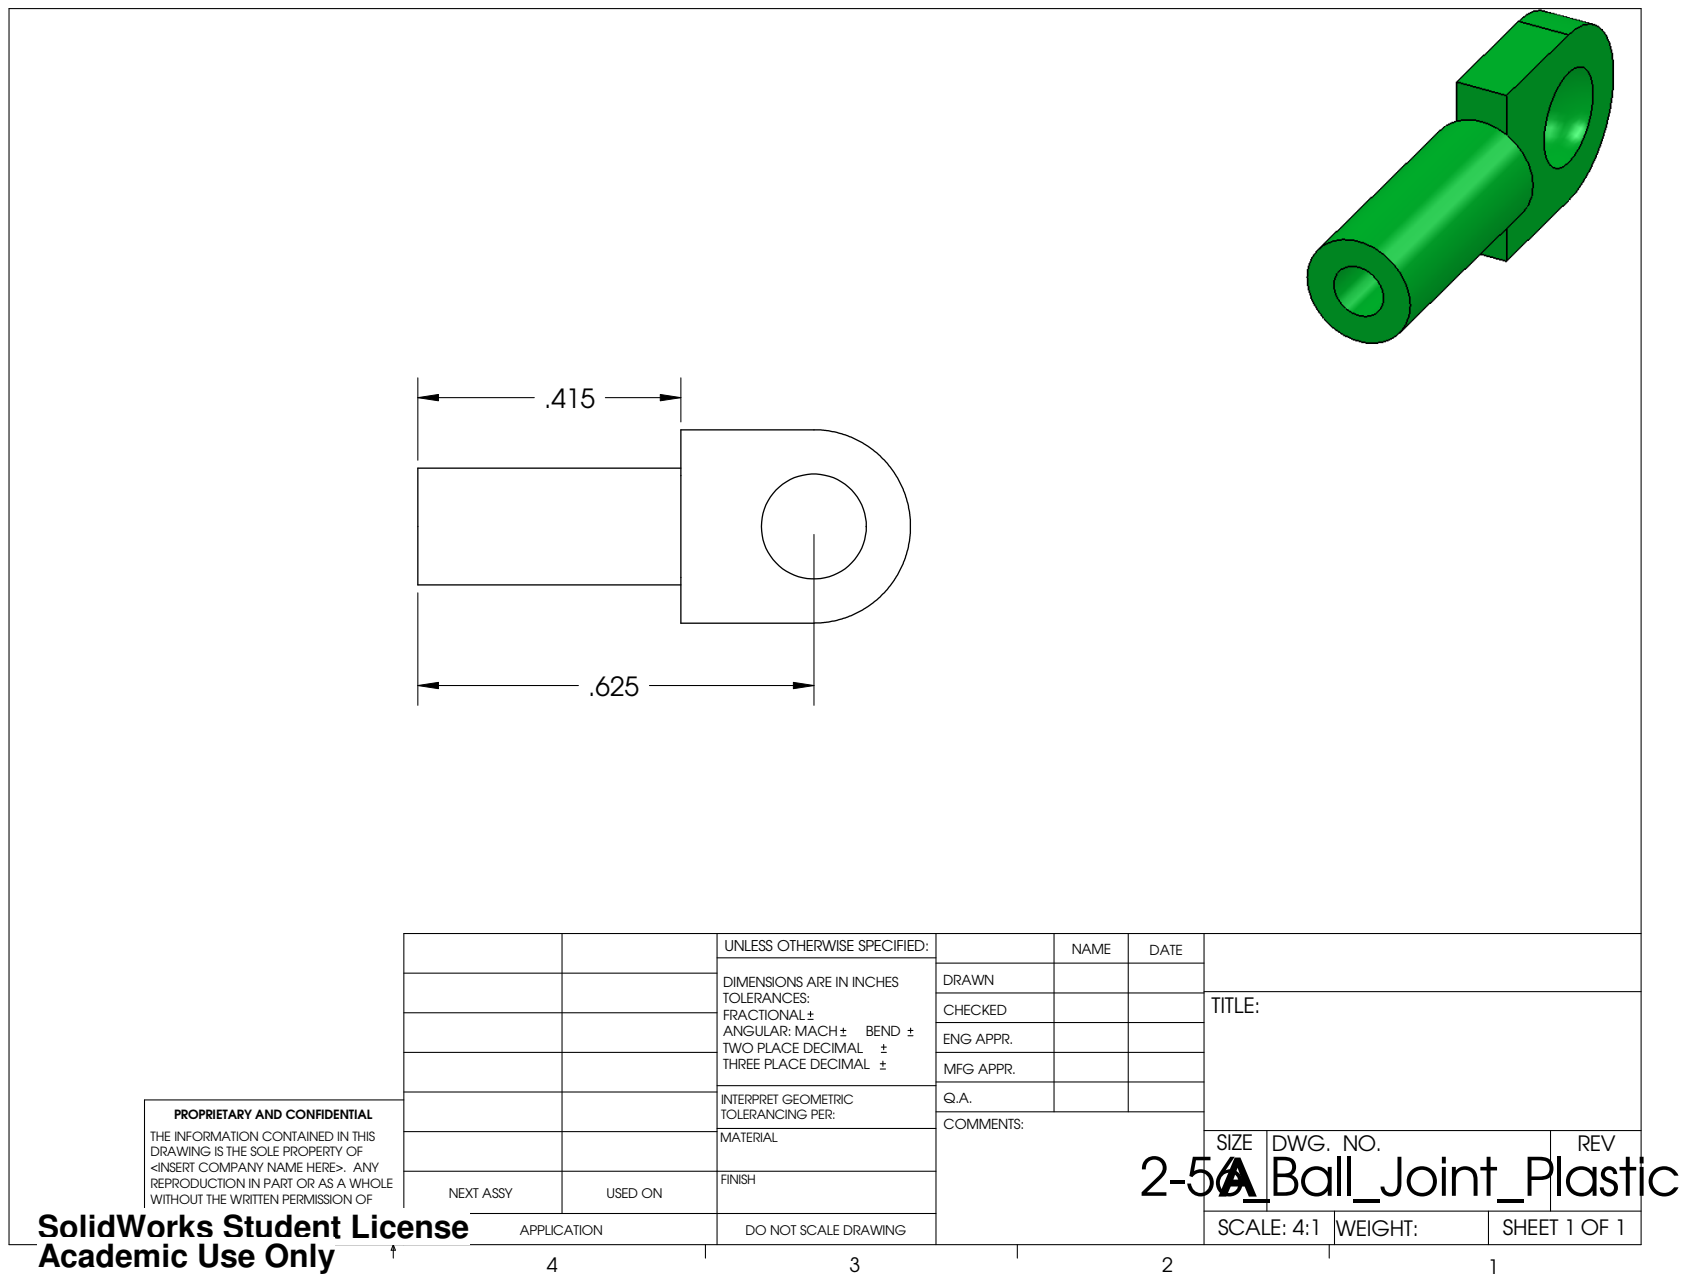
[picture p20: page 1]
2-56_Ball_Joint_Plastic; COMMENTS:; BEND

UNLESS OTHERWISE SPECIFIED: | | NAME | DATE

DIMENSIONS ARE IN INCHES
TOLERANCES:
FRACTIONAL
ANGULAR: MACH
TWO PLACE DECIMAL
THREE PLACE DECIMAL

DRAWN
CHECKED | | | TITLE:

ENG APPR.

MFG APPR.

INTERPRET GEOMETRIC TOLERANCING PER: | Q.A.

PROPRIETARY AND CONFIDENTIAL

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

MATERIAL | | SIZE A | DWG. NO. | REV

NEXT ASSY | USED ON | FINISH

SolidWorks Student License
Academic Use Only

APPLICATION | DO NOT SCALE DRAWING | | SCALE: 4:1 | WEIGHT: | SHEET 1 OF 1

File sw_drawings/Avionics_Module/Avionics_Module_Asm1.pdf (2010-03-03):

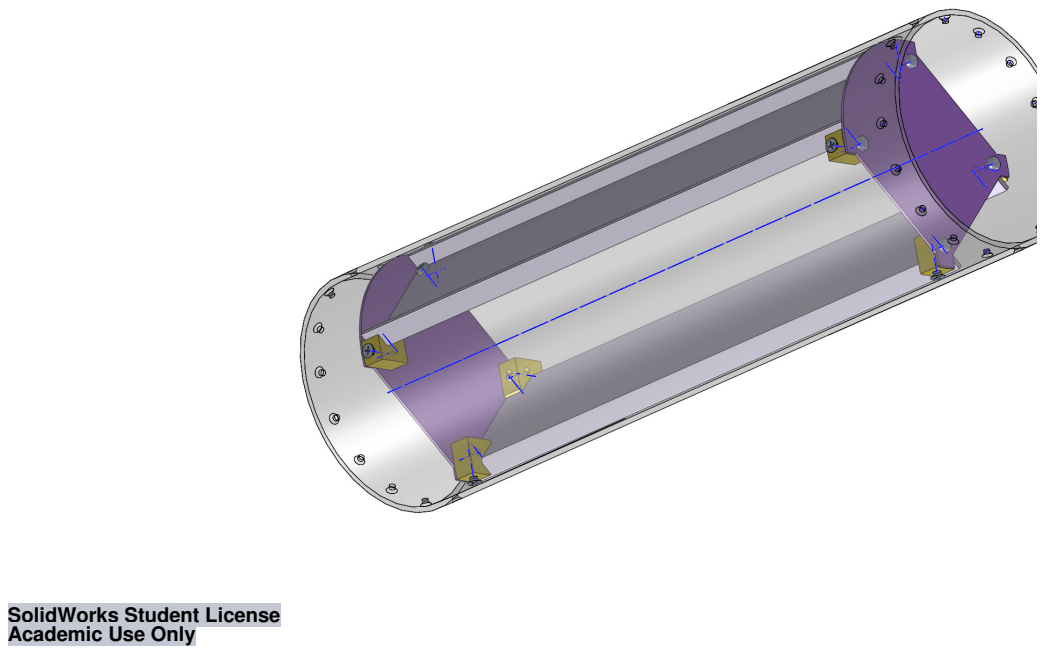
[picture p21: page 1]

SolidWorks Student License
Academic Use Only

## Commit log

2010-03-03 Initial commit of rocket cad drawings
    [0.15in_Spacer.SLDPRT, 0.25-20_1.0in_Allen Head_Cap_Screw_MC-91251A542.SLDPRT, 0.25-20_1.75in_Allen Head_Cap_Screw_MC-91251A548.SLDPRT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]
2010-03-30 added spacers to models for rousetech motor retainer
    [RouseTech_Motor_Retainmenta_Asm.SLDASM, RouseTech_Retainer_Bracket2.SLDASM, RouseTech_Retainer_Spacer.SLDDRW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]
2010-04-22 modifications to retainer spacer
    [ControlArmWithBall.SLDASM, RouseTech_Retainer_Spacer.SLDDRW, RouseTech_Retainer_Spacer.SLDPRT]
2010-04-26 updates to roll control with N2000W reload kit modeled
    [Assembeled.SLDASM, ControlArmWithBall.SLDASM, Data_Logger.SLDPRT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]
2010-05-02 Created BOM and setup mass and material properties for all parts to determin CG, added shield plate, fin clamps, aeroshell
    [0.15in_Spacer.SLDPRT, 0.25-20_1.0in_Allen Head_Cap_Screw_MC-91251A542.SLDPRT, 0.25-20_1.75in_Allen Head_Cap_Screw_MC-91251A548.SLDPRT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]
2010-05-07 Updates to solid model drawings and templates with a few measured mass values
    [Avionics_Module_Plate2.SLDPRT, Cutter.SLDPRT, Drogue_Parachute.SLDPRT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]
2010-05-09 Updates to various solid models with adding weights and more parts
    [6-32_1.25in_Screw_Asm.SLDASM, ARTS2_Flight_Computer_Asm.SLDASM, Aeroshell_18.SLDPRT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]
2010-05-09 added drawing of module for avioncs mounting
    [Module.SLDDRW]
2010-05-13 added mass and vendor info to motor models
    [N2000W_Reload_Assembeled.SLDASM, RouseTech_15360_Motor_Casing.SLDPRT, RouseTech_98mm_Aft_Closure.SLDPRT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]
2010-05-14 adde line cutters to model
    [0.375in_x_0.5in_Hex_Head_Bolt.SLDPRT, 4-40_0.75_Counter_Sunk_Cap_Screw.SLDPRT, 4-40_0.875_Counter_Sunk_Cap_Screw.SLDPRT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]
2010-05-15 Updates to nosecone, TM FC and materials library
    [Nosecone_Asm.SLDASM, Nosecone_Tip.SLDPRT, TeleMetrum.SLDDRW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]
2010-05-18 added initial models of antenna aiming mechanism to solid models
    [Angeling_Bar.SLDPRT, Antenna_Asm.SLDASM, Antenna_Bar.SLDPRT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]
2010-05-18 added more weights to parts and extra fasteners
    [0.375_Hex_Nut.SLDPRT, 0.375_Threaded_Eye_Bolt.SLDPRT, 0.375in-16_2.5in_Bolt.SLDPRT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]
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2010-05-18 Updates to recovery module to add cross bar and defining complete rocket from nosecone tip
    [Assembeled.SLDASM, Avionics_Mid_Plate_Asm.SLDASM, D_Block_5_With_2_Screws_Asm.SLDASM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]
2010-05-24 updates to variosu properties of solid models, added mechanism for aiming antenna on tower
    [2-56_Ball_Joint_Asm.SLDASM, 6-32_1.25in_Screw_Asm.SLDASM, ARTS2_Flight_Computer_Asm.SLDASM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]
2010-05-26 Initial addition of battery case models
    [battery case d1.SLDPRT, battery case d1.STL, battery.SLDPRT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]
2010-06-21 updates to drawings to include more pricing and more properties
    [0.25-20_1.0in_Allen Head_Cap_Screw_MC-91251A542.SLDPRT, 0.25-20_1.75in_Allen Head_Cap_Screw_MC-91251A548.SLDPRT, 0.375in-16_1.25in_Bolt_MC-92620A626.SLDPRT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]
2010-06-23 updates to model properties and mods to match actual flying airframe
    [2-56_Ball_Joint_Asm.SLDASM, 6-32_0.5in_Allen_Head_Cap_Screw_MC-91251A148.SLDPRT, 6-32_1.25in_Screw_Asm.SLDASM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]
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2010-07-03 updated N2000W motor drawings with real weights and dimensions
    [N2000W_Forward_Seal_Disc.SLDPRT, N2000W_Grain.SLDPRT, N2000W_Nozel.SLDPRT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]
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2010-08-29 updates to naming conventions and dimensioning on fin can ratation bearings
    [0.25in_Dowel_Pin.SLDPRT, Full_Fairing_Asm.SLDASM, Full_Fairing_Asm.SLDDRW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]
2010-08-29 updates to full rocket model for rolling fin can
    [Servo_JR_8717.SLDPRT]
2010-09-19 updates to drawings for spinning fin can based on as-machined dimensions
    [0.125in_ball_bearing.SLDPRT, 4-40_0.75in_Allen_Head_Cap_Screw-MC_91251A113.SLDPRT, Full_Fairing_Asm.SLDASM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]
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2010-09-26 added holes to fin clamps for screws and barrel nuts
    [Fin_Clamp_Half.SLDPRT]
2010-09-26 added assembly for launch lug with screws and washers and drawing of lug for fabrication
    [Launch_Lug.SLDDRW, Launch_Lug.SLDPRT, Launch_Lug_Asm.SLDASM]
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2010-09-26 added drawings of motor fairing parts for spin can
    [Motor_Fairing_Lower.SLDDRW, Motor_Fairing_Upper.SLDDRW]
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2010-09-30 integrated Bens battery box into full solid models, sepcified materials and weights in properties
    [Avionics_Module_Asm.SLDASM, Battery_Box_Asm.SLDASM, Battery_Box_Case.SLDPRT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]
2010-09-30 moved location of rotation can launch lug to upper part of spin can
    [Motor_Fairing_Lower.SLDPRT, Outside_Bearing_Frame.SLDPRT]
2010-09-30 added holes for aft motor centering ring on spin can, added launch lug to payload module, fixed hole specifications to be SW tap hole sizes
    [Aft_Motor_Centering_Ring.SLDPRT, Avionics_Module_Asm.SLDASM, Battery_Box_Asm.SLDASM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]
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2010-10-07 updated nosecone with real pusher rod and dimensions of drogue chute
    [Drogue_Parachute.SLDPRT, Nosecone_Asm.SLDASM]
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2010-10-14 updated spin can models to use new cesaroni motor
    [Motor_Fairing_Lower.SLDDRW, Motor_Fairing_Lower.SLDPRT, Motor_Fairing_Upper.SLDDRW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]
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2010-10-14 updates to fin model and drawings based on as-made dimensions
    [Fin.SLDDRW, Fin.SLDPRT, Fin_and_Clamp_Asm.SLDASM]
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2010-10-18 updates to cad drawings based on as-launched model
    [8-32_Eyebolt.SLDPRT, Aft_Motor_Centering_Ring_Thin.SLDDRW, Assembeled.SLDASM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]
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
